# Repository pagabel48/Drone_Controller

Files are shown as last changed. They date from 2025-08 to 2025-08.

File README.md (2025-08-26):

# Drone Controller

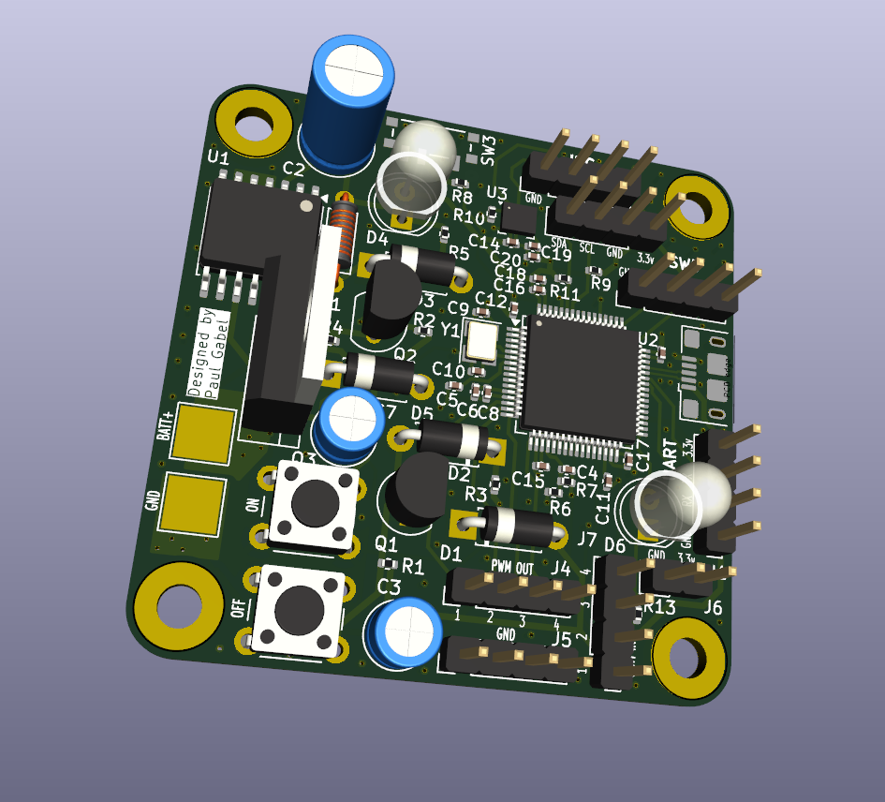
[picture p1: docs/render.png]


The control board is based around an STM32f401 MCU. For power regulation a buck converter is used to generate steady 3.3v from a 4s LiPO Battery or USB 5v line. When powered over battery, the highside power latch allows the board to be toggled on or off.

To allow for closed loop control a BMP280 barometer and an ICM42670P IMU are connected over I2C, and PWM is used to communicate with the motor ESCs and controller receiver. Programming is done over USB, and pins are exposed for UART, I2C, and SWD protocols for extensibility.

Four layers were used to make routing easier and improve signal integrity.

## Routing

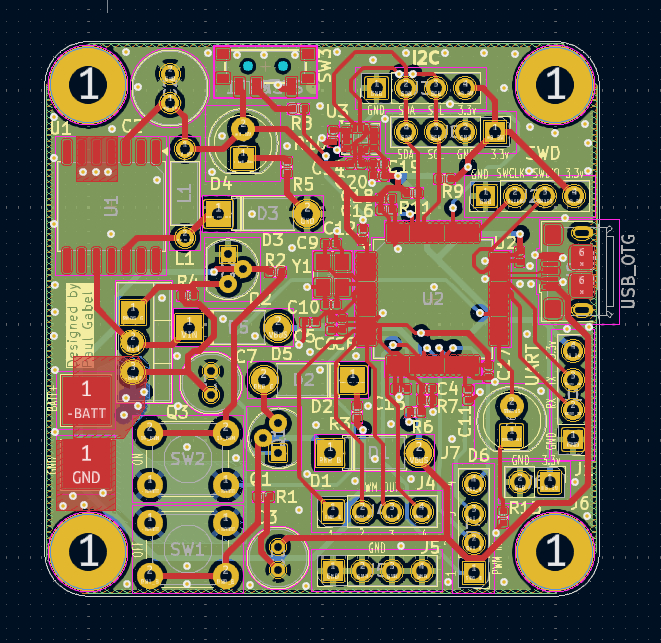
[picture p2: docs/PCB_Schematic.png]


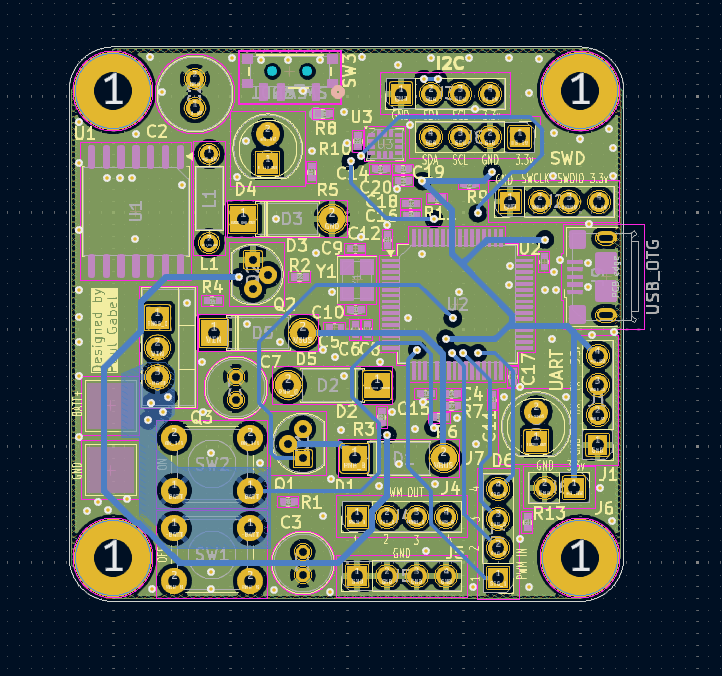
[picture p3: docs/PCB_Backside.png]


## Schematic

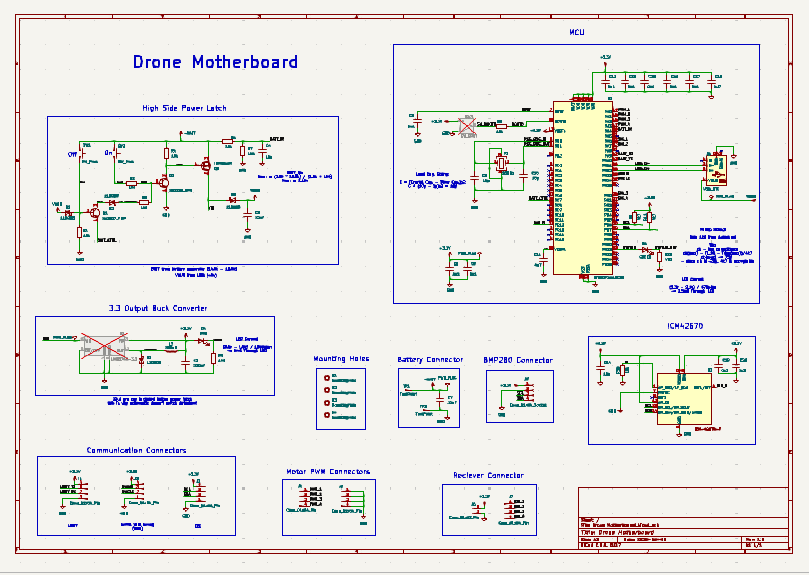
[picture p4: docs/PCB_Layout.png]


# Code

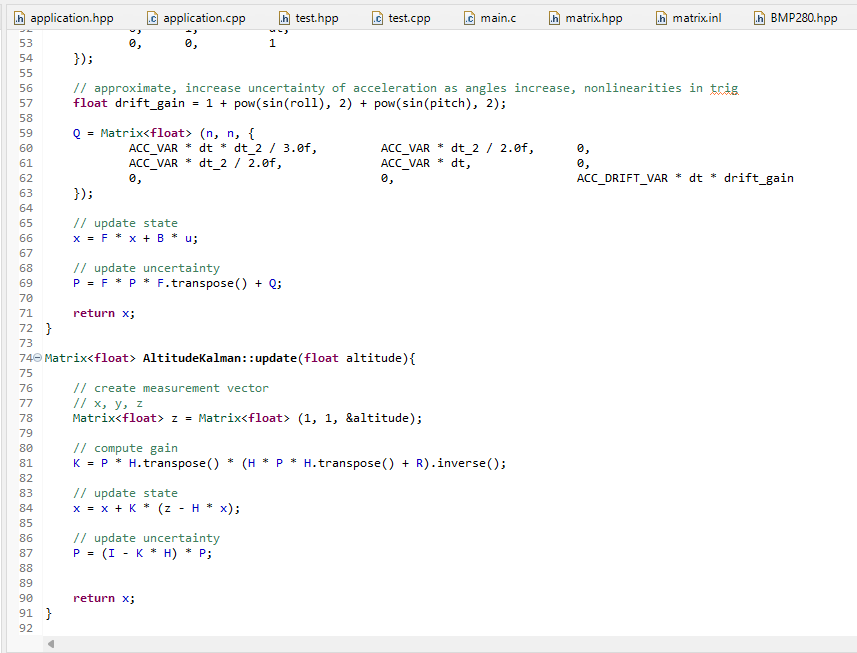
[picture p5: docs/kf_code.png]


State estimation is achieved with two Kalman filters (attitude and altitude), and PID controllers are used in combination with a mixer to get final motor throttle values.

Custom drivers were written to interface with the sensors, and a matrix math library was written using c++ operator overloading - this allows for readable state space control code. The IMU driver reads when triggered by a pin interupt, and the barometer driver uses polling.

A testing routine was written which can be run instead of the main drone loop - it runs unit tests for the code, then tests operation of the sensors, motors, Kalman filters, and status light.

The firmware automatically turns the drone off when the battery voltage drops below a safe level.

Controller Code is Contained in Firmare/Core/

## Code Structure

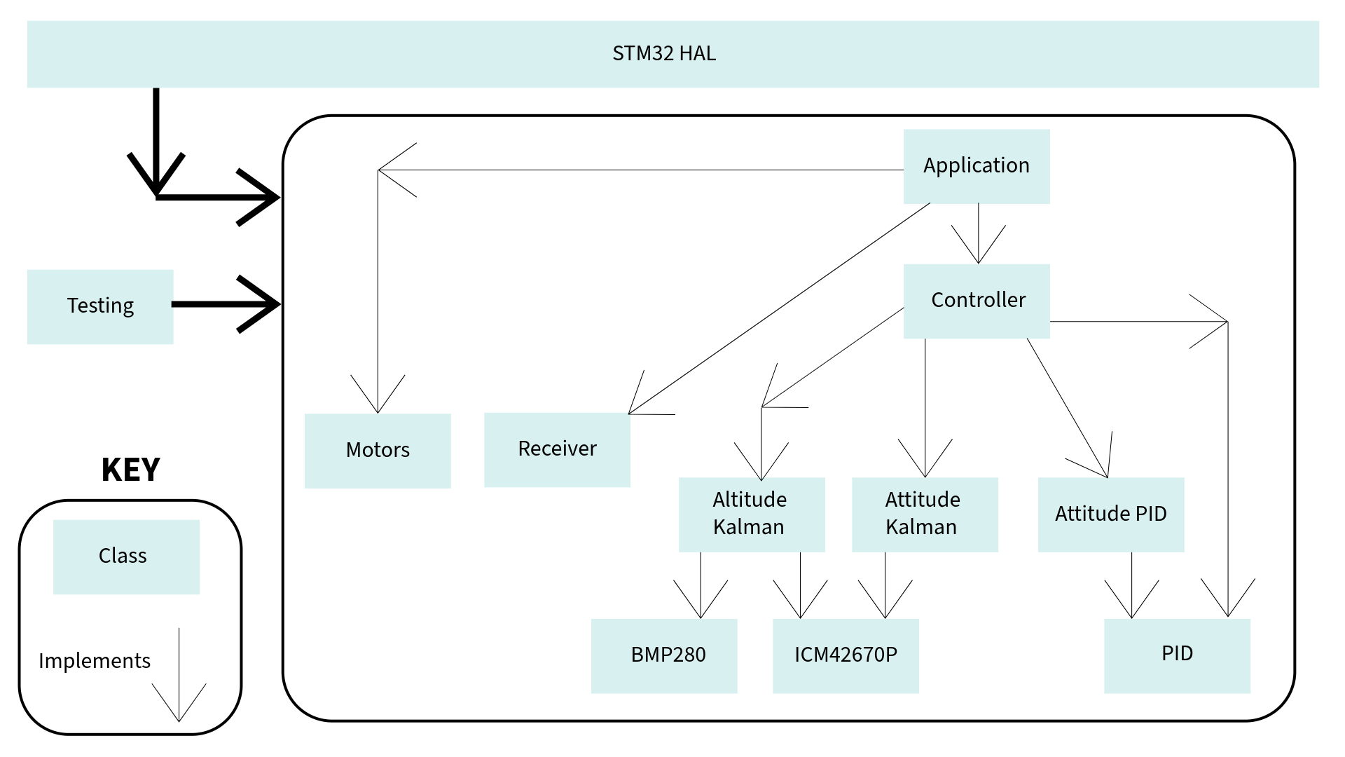
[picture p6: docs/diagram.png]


# Frame

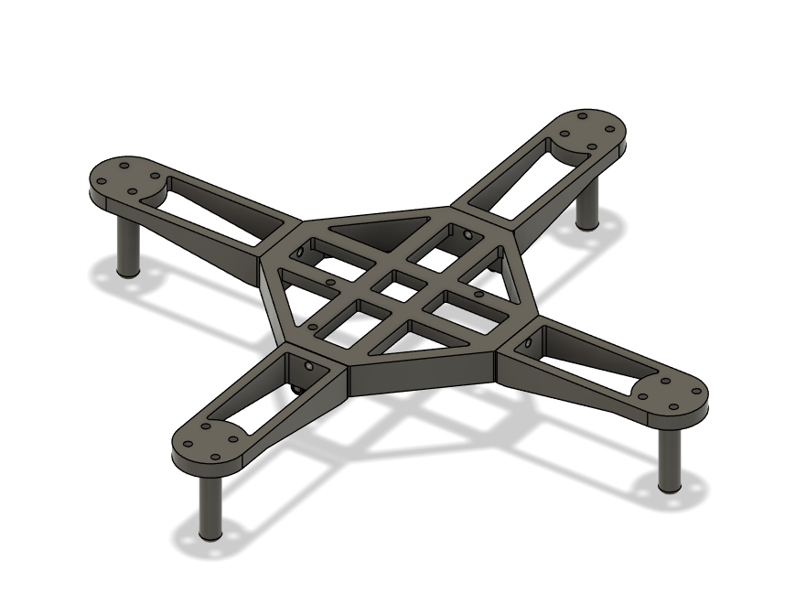
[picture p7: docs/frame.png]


The frame was designed in fusion 360 and was 3d printed using PETG plastic. Care was taken to maximize rigidity whilst minimizing weight.

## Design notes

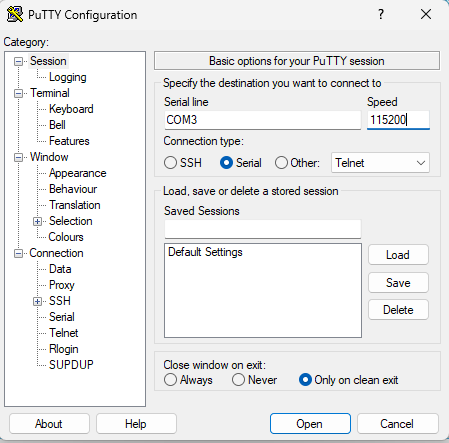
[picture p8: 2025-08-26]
docs/USB_Conn.png

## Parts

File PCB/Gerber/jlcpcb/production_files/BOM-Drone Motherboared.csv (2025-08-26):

Comment | Designator | Footprint | LCSC | Quantity
16MHz | Y1 | Crystal_SMD_3225-4Pin_3.2x2.5mm | C112972 | 1
2u2 | C20,C6 | C_0402_1005Metric | C12530 | 2
USB_OTG | J9 | USB_Micro-B_Amphenol_10118193-0001LF_Horizontal | C132563 | 1
10n | C14,C4 | C_0402_1005Metric | C15195 | 2
0u1 | C12,C13,C15,C16,C17,C19,C5,C8 | C_0402_1005Metric | C1525 | 8
4u7 | C11,C18 | C_0402_1005Metric | C23733 | 2
470 | R13 | R_0402_1005Metric | C25117 | 1
10k | R1,R10,R2,R4,R6,R8 | R_0402_1005Metric | C25744 | 6
1k5 | R3,R5,R7 | R_0402_1005Metric | C25867 | 3
4k7 | R11,R9 | R_0402_1005Metric | C25900 | 2
~ | U3 | LGA-14_3x2.5mm_P0.5mm_LayoutBorder3x4y | C3288646 | 1
10p | C10,C9 | C_0402_1005Metric | C32949 | 2
STM32F401RCT6 | U2 | LQFP-64_10x10mm_P0.5mm | C74524 | 1
TestPoint | TP2 | TestPoint_Pad_4.0x4.0mm |  | 1
LM2574M-3.3 | U1 | SOIC-14W_7.5x9mm_P1.27mm |  | 1
TestPoint | TP1 | TestPoint_Pad_4.0x4.0mm |  | 1
SW_SPDT | SW3 | CUS-12TB_NDC |  | 1
SW_Push | SW2 | SW_PUSH_6mm |  | 1
SW_Push | SW1 | SW_PUSH_6mm |  | 1
IRF9540N | Q3 | TO-220-3_Vertical |  | 1
2N222A_NPN | Q2 | TO-92 |  | 1
2N2907_PNP | Q1 | TO-92 |  | 1
330uH | L1 | L_Axial_L5.3mm_D2.2mm_P7.62mm_Horizontal_Vishay_IM-1 |  | 1
Conn_01x04_Socket | J8 | PinHeader_1x04_P2.54mm_Vertical |  | 1
Conn_01x04_Pin | J3 | PinHeader_1x04_P2.54mm_Vertical |  | 1
Conn_01x04_Pin | J2 | PinHeader_1x04_P2.54mm_Vertical |  | 1
Conn_01x04_Pin | J7 | PinHeader_1x04_P2.54mm_Vertical |  | 1
Conn_01x04_Pin | J1 | PinHeader_1x04_P2.54mm_Vertical |  | 1
Conn_01x02_Pin | J6 | PinHeader_1x02_P2.54mm_Vertical |  | 1
Conn_01x04_Pin | J5 | PinHeader_1x04_P2.54mm_Vertical |  | 1
Conn_01x04_Pin | J4 | PinHeader_1x04_P2.54mm_Vertical |  | 1
GREEN | D6 | LED_D5.0mm_Clear |  | 1
11DQ05 | D5 | D_DO-41_SOD81_P7.62mm_Horizontal |  | 1
RED | D4 | LED_D5.0mm_Clear |  | 1
11DQ05 | D3 | D_DO-41_SOD81_P7.62mm_Horizontal |  | 1
11DQ05 | D2 | D_DO-41_SOD81_P7.62mm_Horizontal |  | 1
11DQ05 | D1 | D_DO-41_SOD81_P7.62mm_Horizontal |  | 1
22uF | C3 | C_Radial_D5.0mm_H5.0mm_P2.00mm |  | 1
22uF | C7 | C_Radial_D5.0mm_H5.0mm_P2.00mm |  | 1
220uF | C2 | C_Radial_D6.3mm_H11.0mm_P2.50mm |  | 1

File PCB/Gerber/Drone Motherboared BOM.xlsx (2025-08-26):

Designator | Quantity | Description | LCSC Part Number | MPN
TP2,TP1 | 2 | TestPoint
Y1 | 1 | 16MHz | C41383241
U3 | 1 | ICM42670P | C3288646
U2 | 1 | STM32F401RCT6 | C74524
U1 | 1 | LM2574M-3.3
SW3 | 1 | SW_SPDT
SW2,SW1 | 2 | SW_Push
R13 | 1 | 470 | C25117
R11,R9 | 2 | 4k7 | C105871
R10,R8,R6,R4,R2,R1 | 6 | 10k | C25744
R7,R5,R3 | 3 | 1k5 | C25867
Q3 | 1 | IRF9540N
Q2 | 1 | 2N222A_NPN
Q1 | 1 | 2N2907_PNP
L1 | 1 | 330uH
J9 | 1 | USB_OTG | C132563
J8 | 1 | Conn_01x04_Socket
J3,J2,J7,J1,J5,J4 | 6 | Conn_01x04_Pin
J6 | 1 | Conn_01x02_Pin
D6 | 1 | GREEN
D5,D3,D2,D1 | 4 | 11DQ05
D4 | 1 | RED
C3,C7 | 2 | 22uF
C18,C11 | 2 | 4u7 | C23733
C17,C19,C16,C15,C13,C12,C8,C5 | 8 | 0u1 | C60474
C20,C6 | 2 | 2u2 | C170151
C14,C4 | 2 | 10n | C60133
C10,C9 | 2 | 10p | C106199
C2 | 1 | 220uF

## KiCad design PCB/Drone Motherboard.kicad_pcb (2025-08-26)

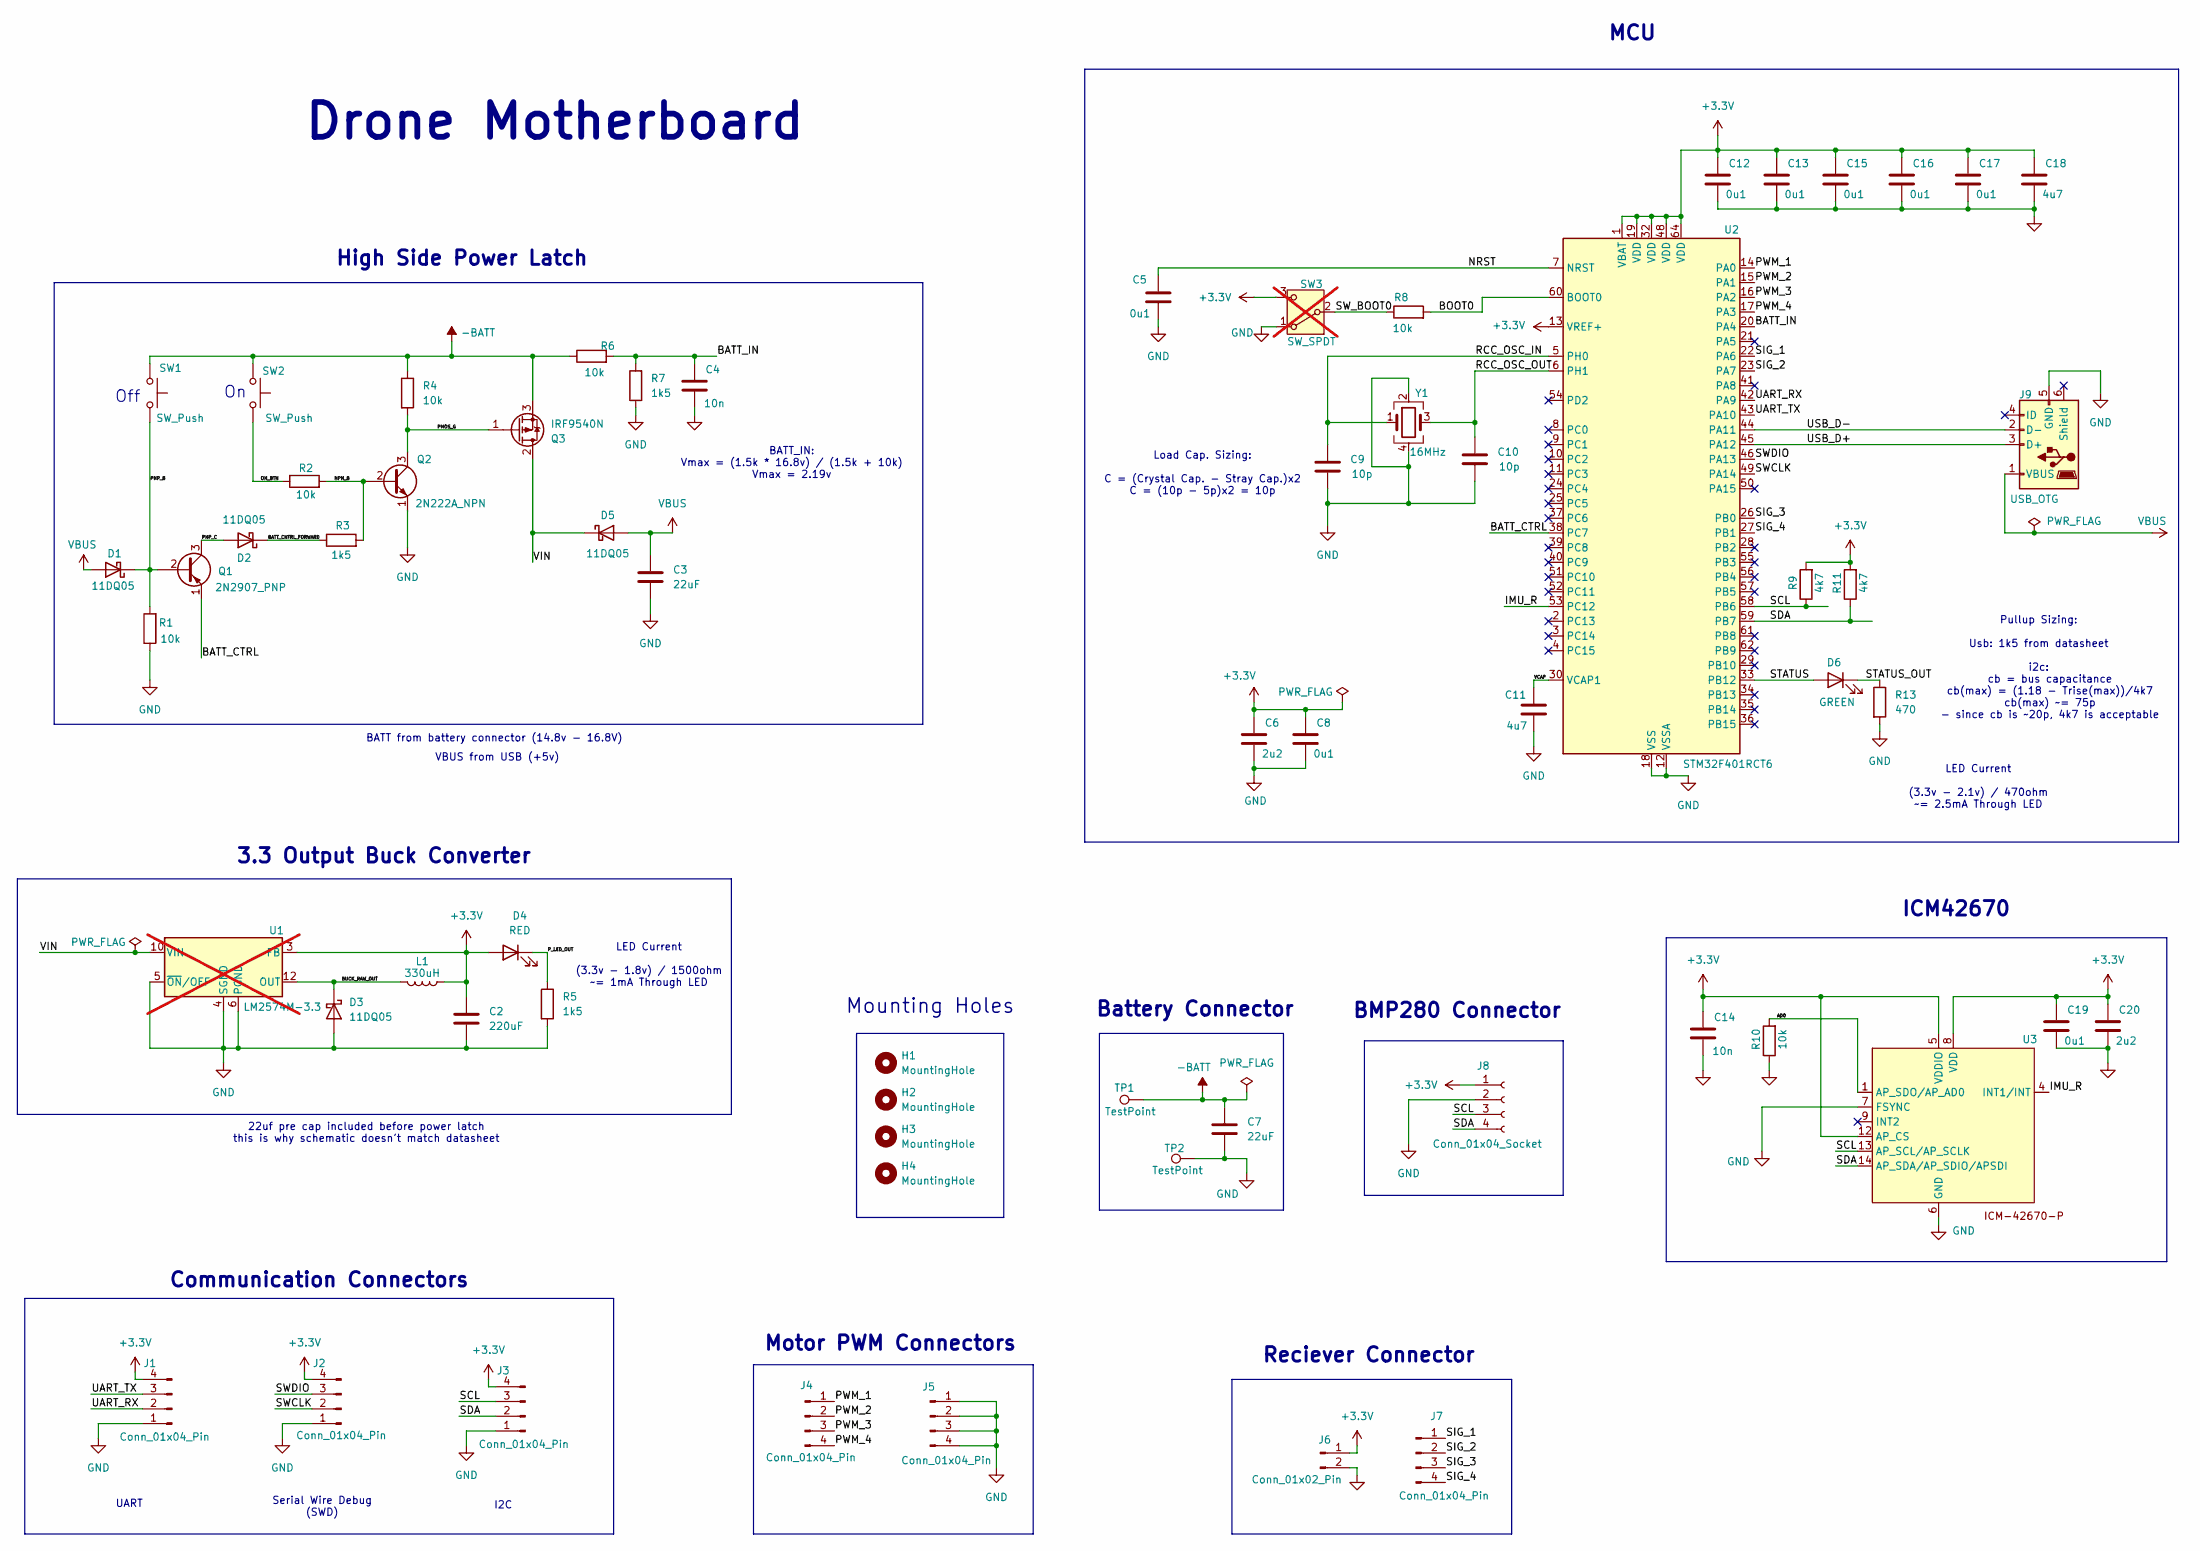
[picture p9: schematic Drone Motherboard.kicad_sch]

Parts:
C2: 220uF; C_Radial_D6.3mm_H11.0mm_P2.50mm
C3, C7: 22uF; C_Radial_D5.0mm_H5.0mm_P2.00mm
C4, C14: 10n; C_0402_1005Metric; LCSC C60133
C5, C8, C12, C13, C15, C16, C17, C19: 0u1; C_0402_1005Metric; LCSC C60474
C6, C20: 2u2; C_0402_1005Metric; LCSC C170151
C9, C10: 10p; C_0402_1005Metric; LCSC C106199
C11, C18: 4u7; C_0402_1005Metric; LCSC C23733
D1, D2, D3, D5: 11DQ05; D_DO-41_SOD81_P7.62mm_Horizontal
D4: RED; LED_D5.0mm_Clear
D6: GREEN; LED_D5.0mm_Clear
H1, H2, H3, H4: MountingHole; MountingHole_3.2mm_M3_Pad
J1, J2, J3, J4, J5, J7: Conn_01x04_Pin; PinHeader_1x04_P2.54mm_Vertical
J6: Conn_01x02_Pin; PinHeader_1x02_P2.54mm_Vertical
J8: Conn_01x04_Socket; PinHeader_1x04_P2.54mm_Vertical
J9: USB_OTG; USB_Micro-B_Amphenol_10118193-0001LF_Horizontal; LCSC C132563
L1: 330uH; L_Axial_L5.3mm_D2.2mm_P7.62mm_Horizontal_Vishay_IM-1
Q1: 2N2907_PNP; TO-92
Q2: 2N222A_NPN; TO-92
Q3: IRF9540N; TO-220-3_Vertical
R1, R2, R4, R6, R8, R10: 10k; R_0402_1005Metric; LCSC C25744
R3, R5, R7: 1k5; R_0402_1005Metric; LCSC C25867
R9, R11: 4k7; R_0402_1005Metric; LCSC C105871
R13: 470; R_0402_1005Metric; LCSC C25117
SW1, SW2: SW_Push; SW_PUSH_6mm
SW3: SW_SPDT; CUS-12TB_NDC; not fitted
TP1, TP2: TestPoint; TestPoint_Pad_4.0x4.0mm
U1: LM2574M-3.3; SOIC-14W_7.5x9mm_P1.27mm; not fitted
U2: STM32F401RCT6; LQFP-64_10x10mm_P0.5mm; LCSC C74524
U3: LGA-14_3x2.5mm_P0.5mm_LayoutBorder3x4y; LCSC C3288646
Y1: 16MHz; Crystal_SMD_3225-4Pin_3.2x2.5mm; LCSC C41383241

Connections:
+3.3V: C2.1, C6.1, C8.1, C12.1, C13.1, C14.1, C15.1, C16.1, C17.1, C18.1, C19.1, C20.1, D4.2 (A), J1.4, J2.4, J3.4, J6.1, J8.1, L1.1, R9.2, R11.2, SW3.3 (C), U1.3 (FB), U2.1 (VBAT), U2.13 (VREF+), U2.19 (VDD), U2.32 (VDD), U2.48 (VDD), U2.64 (VDD), U3.5 (VDDIO), U3.8 (VDD), U3.12 (AP_CS)
-BATT: C7.1, Q3.3 (S), R4.1, R6.1, SW1.1, SW2.1, TP1.1
/AD0: R10.2, U3.1 (AP_SDO/AP_AD0)
/BATT_CNTRL_FORWARD: D2.1 (K), R3.1
/BATT_CTRL: Q1.1 (E), U2.38 (PC7)
/BATT_IN: C4.1, R6.2, R7.2, U2.20 (PA4)
/BOOT0: R8.2, U2.60 (BOOT0)
/BUCK_RAW_OUT: D3.1 (K), L1.2, U1.12 (OUT)
/IMU_R: U2.53 (PC12), U3.4 (INT1/INT)
/NPN_B: Q2.2 (B), R2.2, R3.2
/NRST: C5.1, U2.7 (NRST)
/ON_BTN: R2.1, SW2.2
/PMOS_G: Q2.3 (C), Q3.1 (G), R4.2
/PNP_B: D1.1 (K), Q1.2 (B), R1.2, SW1.2
/PNP_C: D2.2 (A), Q1.3 (C)
/PWM_1: J4.1, U2.14 (PA0)
/PWM_2: J4.2, U2.15 (PA1)
/PWM_3: J4.3, U2.16 (PA2)
/PWM_4: J4.4, U2.17 (PA3)
/P_LED_OUT: D4.1 (K), R5.1
/RCC_OSC_IN: C9.1, U2.5 (PH0), Y1.1
/RCC_OSC_OUT: C10.1, U2.6 (PH1), Y1.3
/SCL: J3.3, J8.3, R9.1, U2.58 (PB6), U3.13 (AP_SCL/AP_SCLK)
/SDA: J3.2, J8.4, R11.1, U2.59 (PB7), U3.14 (AP_SDA/AP_SDIO/APSDI)
/SIG_1: J7.1, U2.22 (PA6)
/SIG_2: J7.2, U2.23 (PA7)
/SIG_3: J7.3, U2.26 (PB0)
/SIG_4: J7.4, U2.27 (PB1)
/STATUS: D6.2 (A), U2.33 (PB12)
/STATUS_OUT: D6.1 (K), R13.1
/SWCLK: J2.2, U2.49 (PA14)
/SWDIO: J2.3, U2.46 (PA13)
/SW_BOOT0: R8.1, SW3.2 (B)
/UART_RX: J1.2, U2.42 (PA9)
/UART_TX: J1.3, U2.43 (PA10)
/USB_D+: J9.3 (D+), U2.45 (PA12)
/USB_D-: J9.2 (D-), U2.44 (PA11)
/VCAP: C11.1, U2.30 (VCAP1)
/VIN: D5.1 (K), Q3.2 (D), U1.10 (VIN)
GND: C2.2, C3.2, C4.2, C5.2, C6.2, C7.2, C8.2, C9.2, C10.2, C11.2, C12.2, C13.2, C14.2, C15.2, C16.2, C17.2, C18.2, C19.2, C20.2, D3.2 (A), J1.1, J2.1, J3.1, J5.1, J5.2, J5.3, J5.4, J6.2, J8.2, J9.5 (GND), Q2.1 (E), R1.1, R5.2, R7.1, R10.1, R13.2, SW3.1 (A), TP2.1, U1.4 (SGND), U1.5 (~ON/OFF), U1.6 (PGND), U2.12 (VSSA), U2.18 (VSS), U2.31 (VSS), U2.47 (VSS), U2.63 (VSS), U3.6 (GND), U3.7 (FSYNC), Y1.2, Y1.4
VBUS: C3.1, D1.2 (A), D5.2 (A), J9.1 (VBUS)

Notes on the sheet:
BATT_IN: Vmax = (1.5k * 16.8v) / (1.5k + 10k) Vmax = 2.19v
Serial Wire Debug (SWD)
I2C
Motor PWM Connectors
ICM42670
Drone Motherboard
BATT from battery connector (14.8v - 16.8V)
VBUS from USB (+5v)
High Side Power Latch
3.3 Output Buck Converter
Load Cap. Sizing: C = (Crystal Cap. - Stray Cap.)x2 C = (10p - 5p)x2 = 10p
UART
Off
BMP280 Connector
MCU
LED Current (3.3v - 1.8v) / 1500ohm ~= 1mA Through LED
Pullup Sizing: Usb: 1k5 from datasheet i2c: cb = bus capacitance cb(max) = (1.18 - Trise(max))/4k7 cb(max) ~= 75p - since cb is ~20p, 4k7 is acceptable
22uf pre cap included before power latch this is why schematic doesn't match datasheet
LED Current (3.3v - 2.1v) / 470ohm ~= 2.5mA Through LED
Battery Connector
Communication Connectors
Reciever Connector
Mounting Holes

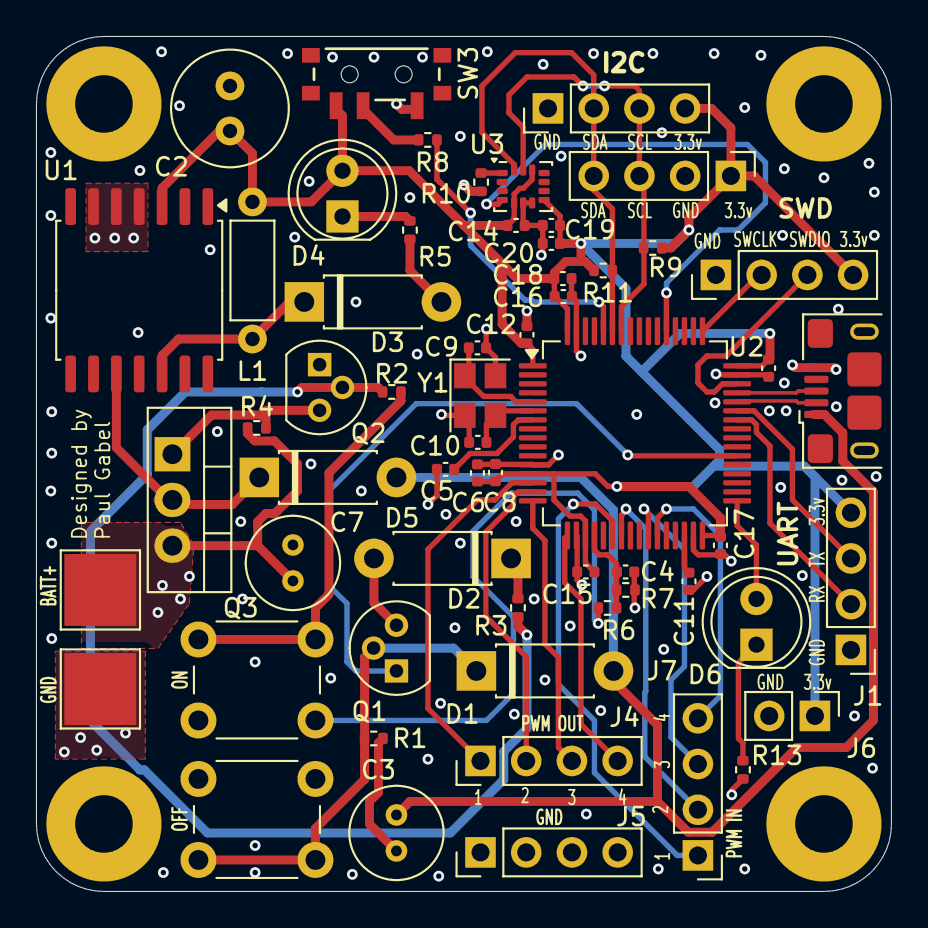
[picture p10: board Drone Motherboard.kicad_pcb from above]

Board: 4 copper layers, 47.5 x 47.5 mm, 63 parts (0 on the bottom side), 41 nets.

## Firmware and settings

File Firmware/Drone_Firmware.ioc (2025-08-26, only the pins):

Mcu.UserName=STM32F401RCTx
PA0-WKUP.Signal=S_TIM2_CH1_ETR
PA1.Signal=S_TIM2_CH2
PA10.Signal=USART1_RX
PA11.Signal=USB_OTG_FS_DM
PA12.Signal=USB_OTG_FS_DP
PA13.Signal=SYS_JTMS-SWDIO
PA14.Signal=SYS_JTCK-SWCLK
PA2.Signal=S_TIM2_CH3
PA3.Signal=S_TIM2_CH4
PA4.Signal=ADCx_IN4
PA6.Signal=S_TIM3_CH1
PA7.Signal=S_TIM3_CH2
PA9.Signal=USART1_TX
PB0.Signal=S_TIM3_CH3
PB1.Signal=S_TIM3_CH4
PB12.GPIO_Label=STATUS
PB12.Signal=GPIO_Output
PB6.Signal=I2C1_SCL
PB7.Signal=I2C1_SDA
PC12.GPIO_Label=IMU_R
PC12.Signal=GPXTI12
PC7.GPIO_Label=BATT_CTRL
PC7.Signal=GPIO_Output

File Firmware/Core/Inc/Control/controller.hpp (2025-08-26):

/*
 * Altitude Kalman Filter
 *
 * Created by Paul Gabel
 * Date: 7/29/2025
 *
 * */

#ifndef CONTROLLER_HPP
#define CONTROLLER_HPP

#include "stm32f4xx_hal.h"

#include "matrix.hpp"
#include "Sensors/ICM42670p.hpp"
#include "Control/pid.hpp"
#include "Control/attitude_pid.hpp"
#include "Control/attitude_kf.hpp"
#include "Control/altitude_kf.hpp"

/*
 * defines
 *
 * */
//bounds for clamping
#define OUTER_LOW_BOUND							0.0f
#define OUTER_UPPER_BOUND						100.0f

#define ANG_VEL_LOW_BOUND					   -50.0f
#define ANG_VEL_UPPER_BOUND						50.0f

/*
 * PID Parameters found through tuning
 *
 * */
// altitude PID parameters
#define ALT_KP									1.0f
#define ALT_KI									1.0f
#define ALT_KD									1.0f

// angular velocity PID parameters
#define VEL_KP									1.0f
#define VEL_KI									1.0f
#define VEL_KD									1.0f

// angle PID parameters
#define ANGLE_KP								1.0f
#define ANGLE_KI								1.0f
#define ANGLE_KD								1.0f

// how much weight to give altitude correction vs. pitch and roll
// pitch, roll weight = (1- MIXING_CONST) / 2
#define MIXING_CONST							0.7f

// range of angle inputs, -45 to 45 degrees in radian
#define ANGLE_INPUT_SENSITIVITY					45.0f

// 3 meters per second possible set point change
#define HEIGHT_INPUT_SENSITIVITY				3.0f

// length of imu burst read
#define IMU_BURST_LENGTH						10

// conversion factor milliseconds to seconds
#define MS_S									0.001f

// holds desired set points from controller
struct control_input {
	float desired_pitch;
	float desired_roll;
	float desired_height;
};

#ifdef __cplusplus

#include <cmath>

/*
 * implements PID and Kalman filter classes
 * ties up loose ends
 *
 * */
class Controller {
public:

	Controller() :

		setpoint(),

		ang_vel_pid_params {
				ANG_VEL_LOW_BOUND,
				ANG_VEL_UPPER_BOUND,
				VEL_KP,
				VEL_KI,
				VEL_KD
		},
		angle_pid_params {
				OUTER_LOW_BOUND,
				OUTER_UPPER_BOUND,
				ANGLE_KP,
				ANGLE_KI,
				ANGLE_KD
		},
		alt_pid_params {
				OUTER_LOW_BOUND,
				OUTER_UPPER_BOUND,
				ALT_KP,
				ALT_KI,
				ALT_KD
		},

		roll_mixing (1, 4, { -1, 1, 1, -1 }),
		pitch_mixing (1, 4, { -1, -1, 1, 1 }),

		altitude_ctrl (alt_pid_params),

		roll_ctrl (ang_vel_pid_params, angle_pid_params),
		pitch_ctrl (ang_vel_pid_params, angle_pid_params),

		alt_skip_time(0)
	{
		// get time in seconds
		last_time = HAL_GetTick() * MS_S;
	}

	/*
	 * generate new motor output from sensor input
	 *
	 * PARAM imu_r: reading from the inertial measurement unit
	 *
	 * returns reference to 4 long array of motor strength percentages
	 *
	 * */
	float* update (motion_reading* imu_r, float time_unacc, float* raw_input);

	/*
	 * generate new motor output from sensor input
	 *
	 * PARAM imu_r: reading from the inertial measurement unit
	 * PARAM height: height reading from the barometer
	 *
	 * returns reference to 4 long array of motor strength percentages
	 *
	 * */
	float* update (motion_reading* imu, float time_unacc, float height, float* raw_input);

private:


	/*
	 * takes array of receiver stick positions and scales to setpoints
	 *
	 * returns a control input struct
	 *
	 * */
	void convert_receiver_input(float* raw_input, float dt);

	/*
	 * mixes the raw pid outputs in each axis to get final motor values
	 *
	 * returns array of desired motor output percentages, for motors 1 : 4
	 *
	 * */
	float* mixer();

	// holds desired setpoints
	control_input setpoint;

	// parameter structs for the pid loops
	pid_params ang_vel_pid_params;
	pid_params angle_pid_params;
	pid_params alt_pid_params;

	// convert desired roll and pitch adjustments to individual motors
	Matrix<float> roll_mixing;
	Matrix<float> pitch_mixing;

	// PID controllers
	PID altitude_ctrl;

	AttitudePID roll_ctrl;
	AttitudePID pitch_ctrl;

	// state estimation
	AttitudeKalman rotation_state;
	AltitudeKalman altitude_state;

	// holds desired motor control values
	float roll_c, pitch_c, alt_c;

	// time stamp of beginning of this measurement period, since IMU readings are burst read
	float last_time;

	// time for altitude update that is skipped due to barometer reading not being available
	float alt_skip_time;
};

#endif
#endif

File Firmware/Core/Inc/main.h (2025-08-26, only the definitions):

#define STATUS_Pin GPIO_PIN_12
#define STATUS_GPIO_Port GPIOB
#define BATT_CTRL_Pin GPIO_PIN_7
#define BATT_CTRL_GPIO_Port GPIOC
#define IMU_R_Pin GPIO_PIN_12
#define IMU_R_GPIO_Port GPIOC
#define IMU_R_EXTI_IRQn EXTI15_10_IRQn
#define STATUS_LED_PIN GPIO_PIN_12
#define STATUS_GPIO_PORT GPIOB

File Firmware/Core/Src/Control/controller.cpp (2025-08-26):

#include "Control/controller.hpp"

float* Controller::update (motion_reading* imu_r, float time_unacc, float* raw_input) {

	// intermediate format to pass accelerometer data from sensor to state estimator
	float ang_vel[2];
	float acc[3];

	// time elapsed over period
	float dt;

	for (int i = 0; i < IMU_BURST_LENGTH; i++) {
		// roll, pitch
		ang_vel[0] = imu_r[i].ang_vel_x;
		ang_vel[1] = imu_r[i].ang_vel_y;

		acc[0] = imu_r[i].acc_x;
		acc[1] = imu_r[i].acc_y;
		acc[2] = imu_r[i].acc_z;

		dt = imu_r[i].elapsed_time;

		rotation_state.predict(ang_vel, dt);
		altitude_state.predict(acc, ang_vel, dt);
	}

	// perform update in the past when reading was taken
	Matrix<float> rot = rotation_state.update(acc);

	// make up for unaccounted time between burst reads
	rotation_state.predict(time_unacc);
	altitude_state.predict(time_unacc);

	// set dt to total time elapsed over period
	float new_time = HAL_GetTick()* MS_S;
	dt = new_time - last_time;

	last_time = new_time;
	alt_skip_time += dt;

	// scale controller input (-1, 1) to set points
	convert_receiver_input (raw_input, dt);

	roll_c = roll_ctrl.update(setpoint.desired_roll, rot(1, 1), imu_r[IMU_BURST_LENGTH - 1].ang_vel_x, dt);
	pitch_c = pitch_ctrl.update(setpoint.desired_pitch, rot(1, 2), imu_r[IMU_BURST_LENGTH - 1].ang_vel_y, dt);

	return mixer();
}

float* Controller::update (motion_reading* imu_r, float time_unacc, float height, float* raw_input) {

	// intermediate format to pass accelerometer data from sensor to state estimator
	float ang_vel[2];
	float acc[3];

	// time elapsed over period
	float dt;

	for (int i = 0; i < IMU_BURST_LENGTH; i++) {
		// roll, pitch
		ang_vel[0] = imu_r[i].ang_vel_x;
		ang_vel[1] = imu_r[i].ang_vel_y;

		acc[0] = imu_r[i].acc_x;
		acc[1] = imu_r[i].acc_y;
		acc[2] = imu_r[i].acc_z;

		dt = imu_r[i].elapsed_time;

		rotation_state.predict(ang_vel, dt);
		altitude_state.predict(acc, ang_vel, dt);
	}

	// perform update in the past when reading was taken
	Matrix<float> rot = rotation_state.update(acc);

	// make up for unaccounted time between burst reads
	rotation_state.predict(ang_vel, time_unacc);
	altitude_state.predict(acc, ang_vel, time_unacc);

	Matrix<float> alt = altitude_state.update(height);

	// set dt to total time elapsed over period
	float new_time = HAL_GetTick()* MS_S;
	dt = new_time - last_time;

	last_time = new_time;

	// scale controller input (-1, 1) to set points
	convert_receiver_input (raw_input, dt);

	roll_c = roll_ctrl.update(setpoint.desired_roll, rot(1, 1), imu_r[IMU_BURST_LENGTH - 1].ang_vel_x, dt);
	pitch_c = pitch_ctrl.update(setpoint.desired_pitch, rot(1, 2), imu_r[IMU_BURST_LENGTH - 1].ang_vel_y, dt);

	alt_c = altitude_ctrl.update(setpoint.desired_height - alt(1, 1), dt + alt_skip_time);

	alt_skip_time = 0;

	return mixer();
}

void Controller::convert_receiver_input(float* raw_input, float dt) {

	// update height setpoint
	setpoint.desired_height += raw_input[0] * HEIGHT_INPUT_SENSITIVITY * dt;

	setpoint.desired_roll = raw_input[1] * ANGLE_INPUT_SENSITIVITY;
	setpoint.desired_pitch = raw_input[2] * ANGLE_INPUT_SENSITIVITY;

}

float* Controller::mixer(){

	float angle_weight = (1.0f - MIXING_CONST) / 2.0f;

	// set throttle component
	float th_base = alt_c * MIXING_CONST;
	// motor 1 2 3 4
	Matrix<float> motors = Matrix<float>(1, 4, {th_base, th_base, th_base, th_base});

	// set roll component
	motors = motors + roll_c * angle_weight * roll_mixing;

	// set pitch component
	motors = motors + pitch_c * angle_weight * pitch_mixing;

	// decompact and return
	float* ret = new float[]{motors(1,1), motors(1,2), motors(1,3), motors(1,4)};
	return ret;
}

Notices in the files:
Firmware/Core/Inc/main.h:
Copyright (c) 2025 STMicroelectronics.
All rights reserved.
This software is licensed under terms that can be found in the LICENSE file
